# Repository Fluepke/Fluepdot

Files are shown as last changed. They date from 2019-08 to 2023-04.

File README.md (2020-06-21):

# Fluepdot
   

**Fluepdot** is a hardware and C project for controlling flip disc panels which where in use by the Berlin public transport operator **[BVG](https://www.bvg.de/en)**.

> This project was shown at [36C3](https://events.ccc.de/congress/2019/wiki/index.php/Main_Page). A large display was constructed from many flipdots. [Pictures](https://www.deutschlandfunkkultur.de/chaos-communication-congress-in-leipzig-auf-den-spuren-von.1264.de.html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) [of](https://foto.benedikt-geyer.de/fluepdot-36c3/) [the](https://www.korrupt.biz/7204/36c3-nachtraege/) [installation](https://www.astrastudio.de/cloud/index.php/apps/gallery/s/nDda9j8dZQ2oNMy#IMG_7059.jpeg).

## Documentation
For **documentation** and a **getting started**, please head over to [https://fluepdot.readthedocs.io/en/latest/](https://fluepdot.readthedocs.io/en/latest/).

## Hardware
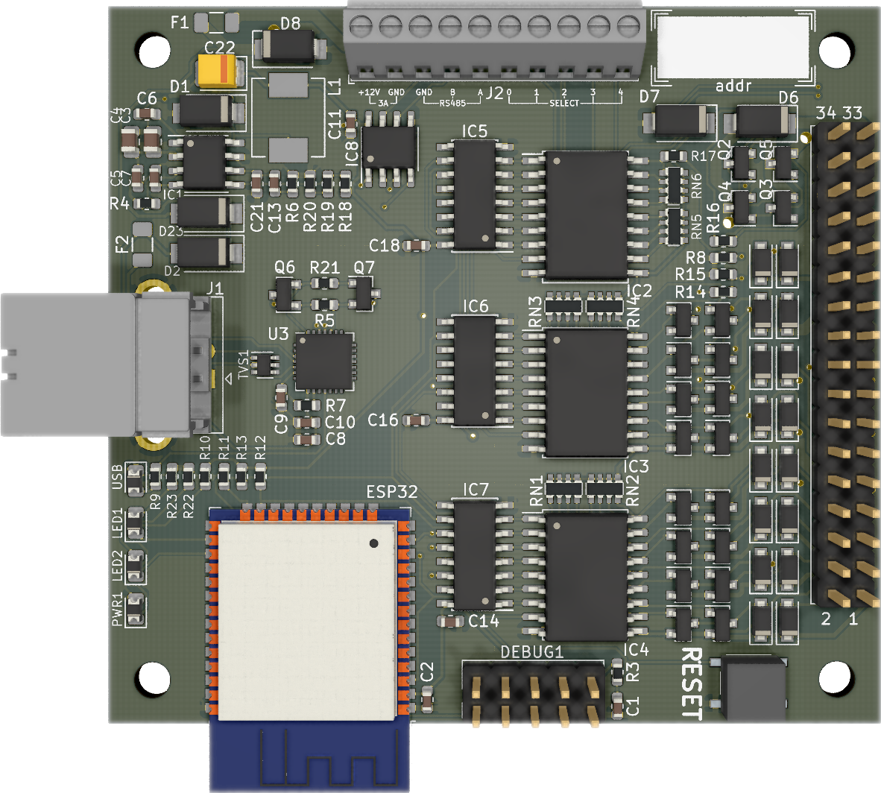
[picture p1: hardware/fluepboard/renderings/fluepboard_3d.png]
PCB 3D rendering


Flipdots and required HW  can be purchased by contacting [fluepdot-sales@luepke.email](mailto:fluepdot-sales@luepke.email).

## Firmware
You can download the latest standalone firmware installer [here](https://gitlab.com/fluepke/fluepdot/-/jobs/artifacts/master/raw/software/service_utility/service_utility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).

## License
Copyright (c) 2020, [@fluepke](http://twitter.com/fluepke) (Fabian Luepke)

Distributed under the terms of the GNU Affero General Public License version 3.

The full license is in the file LICENSE, distributed with this software.

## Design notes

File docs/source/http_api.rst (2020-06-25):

========
HTTP API
========

Framebuffer
===========

For simple integration into your projects, the *fluepboard* firmwares ships with a simple to use HTTP API.

Framebuffer encoding
--------------------

Framebuffers are **ASCII**-encoded. The only allowed characters are **<space>** ``0x20``, **X** ``0x58`` and **``\\n``** ``\0x0A``.

A **bright** (set) pixel is encoded as an X.

A **dark** (cleared) pixel is encoded as a space character.

Each line in a framebuffer has **exactly** the same amount of characters, which is **exactly** the *fluepdot's* width plus one newline character.

Each framebuffer has **exactly** 16 lines.

Lines are terminated by a single ``\n``. No carriage return is used.

Framebuffer manipulations
-------------------------

GET /framebuffer
^^^^^^^^^^^^^^^^
Params
    GET
        **None**
    POST
        **None**

Gets the current framebuffer encoded as explained above.
This endpoint can be used to calculate the framebuffer dimensions, thus there is no seperate endpoint for retrieving the geometry.

POST /framebuffer
^^^^^^^^^^^^^^^^^

Params
    GET
        **None**
    POST
        Raw framebuffer encoded as explained above

Draw the posted framebuffer to the *fluepdot*.

GET /pixel
^^^^^^^^^^

Params
    GET
        x - The x coordinate
        y - The y coordinate

Get the current pixel at the given coordinate encoded as above

POST /pixel
^^^^^^^^^^^

Params
    GET
        x
            The x coordinate (ascii encoded decimal value)
        y
            The y coordinate (ascii encoded decimal value)

Sets the pixel at the given coordinate to bright.

DELETE /pixel
^^^^^^^^^^^^^

Params
    GET
        x
            The x coordinate (ascii encoded decimal value)
        y
            The y coordinate (ascii encoded decimal value)

Set the pixel at the give coordinate to dark.

POST /framebuffer/text
^^^^^^^^^^^^^^^^^^^^^^

Params
    POST
        Text to display
    GET
        x
            The x coordinate to render text to
        y
            The y coordinate to render text to
        font
            The font's name to use for rendering text. Retrieve a list of fonts at `GET /fonts`

Render a string

GET /fonts
^^^^^^^^^^

Returns a list of installed fonts

For each font there are two lines: First the **full_name** and then **short_name** which is used with the `POST /framebuffer/text` eAPI endpoint.

Rendering options
=================

Rendering mode
--------------

GET /rendering/mode
^^^^^^^^^^^^^^^^^^^

Retuns an ASCII printed integer which value is defined as follows:

    .. doxygenenum:: flipdot_rendering_mode_t
       :project: fluepdot

PUT /rendering/mode
^^^^^^^^^^^^^^^^^^^
Params
    GET
        **None**
    POST
        ASCII printed integer, which value is to be interpreted as stated above.

Rendering timings encoding
--------------------------

Rendering timings are **ASCII**-encoded. The only allowed characters are 0-9 (``0x30-0x39``) and ``\\n``.

For each *fluepdot* column, there are **exactly** 3 rows:

1. **Pre delay**
   
    How long to wait (50 microseconds steps) before rendering to the column.

2. **Clear delay**

    How long to power the coils in order to clear the column (in 50 microseconds steps).

3. **Set delay**

    How long to power the coils in order to set the column (in 50 microseconds steps)

Each line has **exactly** 5 characters and one trailing ``\\n``. You have to pad with zeros.
Each line contains the decimal value in ascii-encoded form.

.. warning::

   Powering a coil repeatedly for a long duration *might* cause the coil to overheat and or fail.
   Decreasing the timings might result in higher **framerate**, but might result in not all pixels flipping.

   Usually **1600uS** are enough to reliably flip all pixels.
   This is the **default**.

GET /rendering/timings
^^^^^^^^^^^^^^^^^^^^^^

Returns the timing configuration encoded as explained above.

POST /rendering/timings
^^^^^^^^^^^^^^^^^^^^^^^

Params
    GET
        None
    POST
        Timing configuration as explained above.

Set the timing configuration.

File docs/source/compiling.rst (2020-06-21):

Compiling
=========

A multistage **Docker** environment is used to build firmware and documentation.

1. Clone the repository *recursively*.

   .. code:: bash

        git clone --recursive https://gitlab.com/fluepke/fluepdot.git

2. Build or pull the build container.

    * If you have a high bandwidth internet connection downloading is fastest (~ 10 GB):

        .. code:: bash
    
            docker pull fluepke/fluepdot-build-environment

    * If you have a low bandwidth internet connection building is faster (still ~ 3 GB)

        .. code:: bash
            
            docker build --force-rm -t fluepke/fluepdot-build-environment -f Dockerfile .

3. Build the second stage container

        .. code:: bash

            docker build --force-rm -t fluepdot -f Dockerfile.build .

4. Run the second stage container and flash the image (assuming your flipdot's serial device is at ``/dev/ttyUSB0``)

        .. code:: bash
           
            docker run -d --name fluepdot --device /dev/ttyUSB0:/fluepdot-device:rwm
            docker exec -it fluepdot \
                -w "/fluepdot/software/firmware" \
                -e ESPTOOL_PORT='/fluepdot-device' \
                -e ESPTOOL_BAUD='480000' \
                make flash

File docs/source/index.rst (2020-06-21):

.. Copyright (c) 2020, @fluepke (Fabian Luepke)

  Distributed under the terms of the GNU Affero General Public License version 3.

  The full license is in the file LICENSE, distributed with this software.




Hardware project for controlling legacy flipdot panels used by `BVG`_

Introduction
============

.. note::
   This project was exhibited at `36C3`_. A large display was constructed from many flipdots. `Pictures`_ `of`_ `the`_ `installation`_.

`fluepdot` is a hardware and C project for controlling flip disc panels which where in use by the Berlin public transport operator `BVG`_.

Hardware
--------
Up to 5 flipdot panels are managed by one *fluepboard*.
It is equipped with a dual core **ESP32** that supports **WLAN** and **Bluetooth**.
An **RS485** transceiver can be used for wired installations.
You only have to solder the THT (through hole technology) connectors which are shipped together with the fluepboard as a kit.

+----------+----------+
|     Top  |  Bottom  |
+----------+----------+
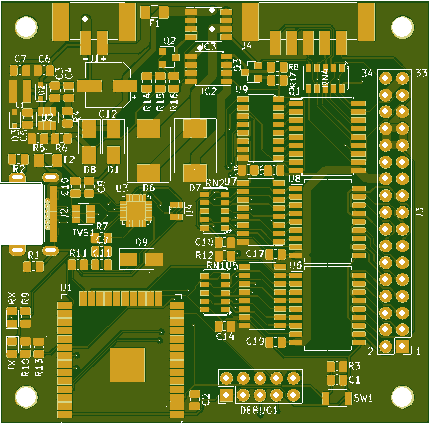
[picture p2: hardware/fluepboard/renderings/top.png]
PCB top layer
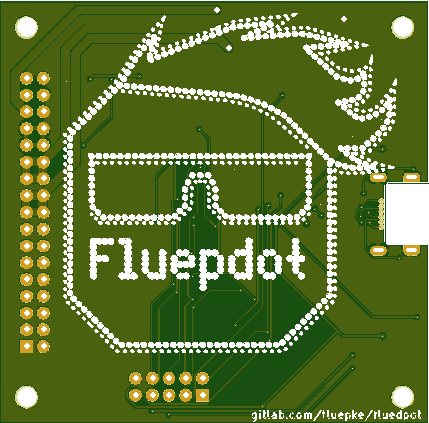
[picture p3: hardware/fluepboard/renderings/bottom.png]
PCB bottom layer
|     |  |
+----------+----------+

Software
--------
The *fluepboard* comes pre-flashed with a firmware, that allows for various ways of interacting with the flipdot.

Features:

- CLI for configuration and testing purposes
- mDNS for simple service discovery
- HTTP API for framebuffer manipulations
- SNMP for monitoring and framebuffer manipulations
- BT LE support for framebuffer manipulations
- C flipdot library for custom applications

.. toctree ::
   :caption: USAGE

   getting_started
   command_line
   snmp
   http_api

.. toctree ::
   :caption: FIRMWARE

   firmware_update

.. toctree ::
   :caption: DEVELOPER ZONE
   :maxdepth: 2

   compiling
   flipdot_library

.. _BVG: https://www.bvg.de/en
.. _36C3: https://events.ccc.de/congress/2019/wiki/index.php/Main_Page
.. _Pictures: https://www.deutschlandfunkkultur.de/chaos-communication-congress-in-leipzig-auf-den-spuren-von.1264.de.html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
.. _of: https://foto.benedikt-geyer.de/fluepdot-36c3/
.. _the: https://www.korrupt.biz/7204/36c3-nachtraege/
.. _installation: https://www.astrastudio.de/cloud/index.php/apps/gallery/s/nDda9j8dZQ2oNMy#IMG_7059.jpeg

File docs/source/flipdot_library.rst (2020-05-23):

Flipdot API reference
=====================

Flipdot
-------

Flipdot structs
^^^^^^^^^^^^^^^

.. doxygenstruct:: flipdot_t
   :project: fluepdot
   :members:

.. doxygenstruct:: flipdot_panel_t
   :project: fluepdot
   :members:

.. doxygenstruct:: flipdot_configuration_t
   :project: fluepdot
   :members:

Flipdot functions
^^^^^^^^^^^^^^^^^

.. doxygenfunction:: flipdot_initialize
   :project: fluepdot

.. doxygenfunction:: flipdot_set_power
   :project: fluepdot

.. doxygenfunction:: flipdot_get_power
   :project: fluepdot

.. doxygenfunction:: flipdot_set_dirty_flag
   :project: fluepdot

Framebuffer
-----------

Framebuffer struct
^^^^^^^^^^^^^^^^^^^
.. doxygenstruct:: framebuffer_t
   :project: fluepdot
   :members:

.. doxygenfunction:: flipdot_framebuffer_init
   :project: fluepdot

.. doxygenfunction:: flipdot_framebuffer_free
   :project: fluepdot

Framebuffer manipulation
^^^^^^^^^^^^^^^^^^^^^^^^
.. doxygenfunction:: flipdot_framebuffer_clear
   :project: fluepdot

.. doxygenfunction:: flipdot_framebuffer_get_pixel
   :project: fluepdot

.. doxygenfunction:: flipdot_framebuffer_set_pixel
   :project: fluepdot

Framebuffer de/encoding
^^^^^^^^^^^^^^^^^^^^^^^
.. doxygenfunction:: flipdot_framebuffer_encode_line
   :project: fluepdot

.. doxygenfunction:: flipdot_framebuffer_decode_line
   :project: fluepdot

.. doxygenfunction:: flipdot_framebuffer_encode_pixel
   :project: fluepdot

.. doxygenfunction:: flipdot_framebuffer_decode_pixel
   :project: fluepdot

.. doxygenfunction:: flipdot_framebuffer_printf
   :project: fluepdot

Framebuffer diffing
^^^^^^^^^^^^^^^^^^^

.. doxygenfunction:: flipdot_framebuffer_compare
   :project: fluepdot

.. doxygenfunction:: flipdot_framebuffer_compare_partial
   :project: fluepdot

Rendering options
-----------------

.. doxygenstruct:: flipdot_rendering_options_t
   :project: fluepdot
   :members:

.. doxygenstruct:: flipdot_rendering_delay_options_t
   :project: fluepdot
   :members:

.. doxygenenum:: flipdot_rendering_mode_t
   :project: fluepdot

.. doxygenfunction:: flipdot_rendering_options_initialize
   :project: fluepdot

.. doxygenfunction:: flipdot_rendering_options_copy
   :project: fluepdot

.. doxygenfunction:: flipdot_rendering_options_free
   :project: fluepdot

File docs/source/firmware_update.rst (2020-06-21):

Firmware update
===============

Using service utility
---------------------

The *fluepboard*'s firmware can be easily updated using a **standalone** binary for GNU/Linux (amd64) that is generated by the *Gitlab CI* build process of this project.

You can get the latest version `here`_.

Make sure your current user has permission to use the serial port (in this example `/dev/ttyUSB0`), then run:

    .. code:: bash

        ./service_utility -serial.port /dev/ttyUSB0

This utility will flash:
* the partition table
* the bootloader
* the factory application

Using esptool.py
----------------

You can also flash the firmware using `esptool.py`_. `Download`_ and unpack the compiled firmware, then run:

    .. code:: bash

        esptool.py --chip esp32 --before=default_reset --after=hard_reset write_flash --flash_mode dio --flash_freq 40m --flash_size 4MB 0x8000 partition_table/partition-table.bin 0x1000 bootloader/bootloader.bin 0x10000 flipdot-firmware.bin

.. _here: https://gitlab.com/fluepke/fluepdot/-/jobs/artifacts/master/raw/software/service_utility/service_utility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
.. _esptool.py: https://github.com/espressif/esptool
.. _Download: https://gitlab.com/fluepke/fluepdot/-/jobs/artifacts/master/download?job=build_esp32_image

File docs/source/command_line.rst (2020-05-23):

Commandline interface
=====================

For debugging and configuration purposes the *fluepboard* firmware provides a simple CLI.

The serial interface is available by connecting the *fluepboard* to a computer via USB.

Serial interface works at 115200/8-N-1 [#]_.

.. note::
   
    After performing configuration changes, please issue a ``config_save`` followed by a ``reboot`` in order to apply the configuration.

Available commands
------------------

Type ``help`` to get a list of available commands:

.. code:: bash

    help
      Print the list of registered commands
    
    ping  [-W <t>] [-i <t>] [-s <n>] [-c <n>] [-Q <n>] <host>
      send ICMP ECHO_REQUEST to network hosts
      -W, --timeout=<t>  Time to wait for a response, in seconds
      -i, --interval=<t>  Wait interval seconds between sending each packet
      -s, --size=<n>  Specify the number of data bytes to be sent
      -c, --count=<n>  Stop after sending count packets
      -Q, --tos=<n>  Set Type of Service related bits in IP datagrams
            <host>  Host address
    
    host  <host>
      Perform a DNS lookup
            <host>  Host to look up
    
    traceroute  <host>
      Perform a traceroute
            <host>  Host to traceroute
    
    reboot
      Perform a software reset
    
    show_version
      Get version of chip and SDK
    
    show_tasks
      Get information about running tasks
    
    config_save
      Save the current system configuration to flash
    
    config_load
      Load the system configuration from flash
    
    config_show
      Show the current system configuration
    
    config_reset
      Factory reset the system configuration
    
    config_wifi_ap  <ssid> [<password>]
      Configure AP mode
            <ssid>  WiFi SSID
        <password>  WiFi Password
    
    config_wifi_station  <ssid> [<password>]
      Configure station mode
            <ssid>  WiFi SSID
        <password>  WiFi Password
    
    config_hostname  <hostname>
      Set system hostname
        <hostname>  Hostname
    
    config_panel_layout  <panel_size> [<panel_size>]...
      Configure panel count and sizes
      <panel_size>  Panel size
    
    flipdot_clear  [--invert]
      Clear the flipdot
          --invert  Set all pixels to white instead of black
    
    show_fonts
      List installed fonts
    
    render_font  [-x <int>] [-y <int>] [-f <font>] <text>
      Render some text given some font
      -x, --X=<int>  Depending on aligned, either left, center or right edge of target.
      -y, --Y=<int>  Upper edge of the target area.
      -f, --font=<font>  Name of font to use
            <text>  Text to display
    
Usage examples
--------------

- Connect to a wireless network

    .. code:: bash
    
       config_wifi_station NetworkName Password
       config_show
       config_save
       reboot

- Connect to an unencrypted wireless network

    .. code:: bash
    
       config_wifi_station NetworkName
       config_show
       config_save
       reboot

- MTU test

    .. code:: bash

        ping fritz.box -s 1472

- Cycle all pixels

    .. code:: bash

        flipdot_clear
        flipdot_clear --invert

Footnotes
---------

.. [#] See https://en.wikipedia.org/wiki/8-N-1

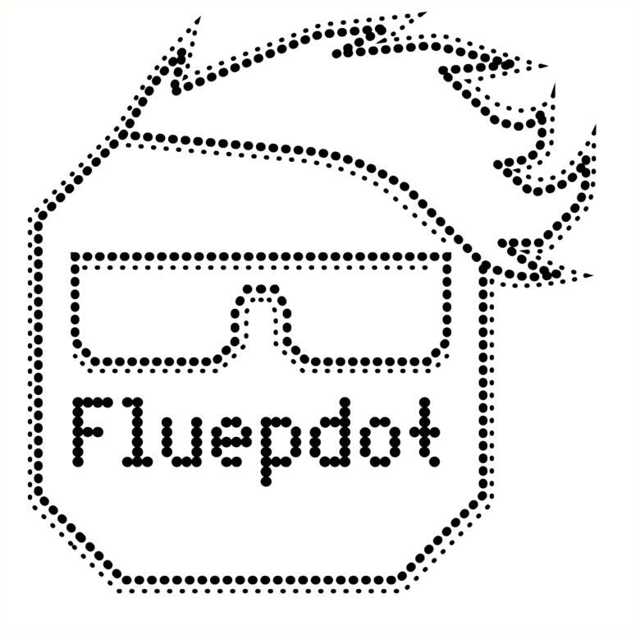
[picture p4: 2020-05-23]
artwork/output.png

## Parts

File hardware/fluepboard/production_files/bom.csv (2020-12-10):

Comment | Designator | Footprint | LCSC | LCSC | Octopart | Description | Extended Part | Manufacturer | Height | LCSC Price/Stock | Manufacturer_Name | Manufacturer_Part_Number | Category | DK_Datasheet_Link | DK_Detail_Page | Digi-Key_PN | Family | MPN | status | Status
100nF | C1,C2,C11,C6,C9,C8,C18,C16,C14 | Capacitor_SMD:C_0603_1608Metric |  | C14663 | C0805C104Z5VACTU | MULTILAYER CERAMIC CAPACITORS MLCC - SMD/SMT 100NF 50V 0603 ROHS | 0 | CC0603KRX7R9BB104
1uF | C10 | Capacitor_SMD:C_0603_1608Metric |  | C15849 |  | MULTILAYER CERAMIC CAPACITORS MLCC - SMD/SMT 1UF 50V 0603 ROHS | 0 | CL10A105KB8NNNC
1nF | C13 | Capacitor_SMD:C_0603_1608Metric |  | C1588 |  | MULTILAYER CERAMIC CAPACITORS MLCC - SMD/SMT 1NF 50V 0603 ROHS | 0 | CL10B102KB8NNNC
47pF | C21 | Capacitor_SMD:C_0603_1608Metric |  | C1671 |  | MULTILAYER CERAMIC CAPACITORS MLCC - SMD/SMT 47PF 50V 0603 ROHS | 0 | CL10C470JB8NNNC
100uF | C22 | Capacitor_Tantalum_SMD:CP_EIA-3528-21_Kemet-B |  | C16133 |  | TANTALUM CAPACITORS 100UF 6.3V CASE-B_3528 ROHS | 0 | TAJB107K006RNJ
4.7uF | C4,C3 | Capacitor_SMD:C_0805_2012Metric |  | C1779 |  | MULTILAYER CERAMIC CAPACITORS MLCC - SMD/SMT 4.7UF 25V 0805 ROHS | 0 | CL21A475KAQNNNE
10nF | C5,C7 | Capacitor_SMD:C_0603_1608Metric |  | C57112 |  | MULTILAYER CERAMIC CAPACITORS MLCC - SMD/SMT 10NF 50V 0603 ROHS | 0 | 0603B103K500NT
SS14 | D2,D23 | Diode_SMD:D_SMA |  | C2480 |  | SCHOTTKY BARRIER DIODES (SBD) SMA(DO-214AC) ROHS | 0 | SS14
SM4007PL | D3,D9,D11,D13,D15,D17,D19,D21,D5,D10,D12,D14,D16,D18,D20,D22 | Diode_SMD:D_SOD-123F |  | C64898 |  |  |  | SM4007PL
USB | D4 | Diode_SMD:D_0805_2012Metric |  | C2296 | SML-211YTT86 | LIGHT EMITTING DIODES (LED) YELLOW 592~594NM 95~113MCD@20MA TOP VIEW 0805 ROHS | 0 | 17-21SUYC/TR8
SS34 | D8,D1,D6,D7 | Diode_SMD:D_SMA |  | C84635 | B140-E3/61T | SCHOTTKY BARRIER DIODES (SBD) SMA(DO-214AC) ROHS | 0 | SS34
Conn_02x05_Counter_Clockwise | DEBUG1 | Connector_PinHeader_2.54mm:PinHeader_2x05_P2.54mm_Vertical |  |  | Molex 10-89-7101
ESP32-WROOM-32 | ESP32 | RF_Module:ESP32-WROOM-32 |  | - | ESP32-WROOM-32
3A | F1 | Fuse:Fuse_1206_3216Metric |  | C182441 |  | SURFACE MOUNT FUSES 1206 ROHS | 1 | 12D1300C
500mA | F2 | Fuse:Fuse_1206_3216Metric |  | C69688 | 3413.0113.22 | PTC RESETTABLE FUSES 1206 ROHS | 1 | nSMD050
MountingHole | H1,H3,H4,H2 | MountingHole:MountingHole_3.2mm_M3_ISO7380
TPS54331DR | IC1 | Package_SO:SOIC-8_3.9x4.9mm_P1.27mm |  | C9865 |  | DC-DC CONVERTERS STEP-DOWN ADJUSTABLE 1 3.5V 28V 0.8V 25V 3A SOIC-8_150MIL ROHS | 0 | TPS54331DR
ULN2803ADWR | IC2,IC4,IC3 | Package_SO:SOIC-18W_7.5x11.6mm_P1.27mm |  | C9683 | ULN2803ADW | TRANS 8NPN DARL 50V 0.5A 18SO | 0 | ULN2803ADWR |  |  |  |  | Discrete Semiconductor Products | http://www.ti.com/lit/ds/symlink/uln2803a.pdf | /product-detail/en/texas-instruments/ULN2803ADWR/296-15777-1-ND/598088 | 296-15777-1-ND | Transistors - Bipolar (BJT) - Arrays | ULN2803ADWR | review
74HCT595 | IC7,IC6,IC5 | Package_SO:SOIC-16_3.9x9.9mm_P1.27mm |  | C5947 | MC74HC595ADG |  | 0
SP3485EN | IC8 | Package_SO:SOIC-8_3.9x4.9mm_P1.27mm |  | C8963 |  |  | 0 | CP2102-GMR
USB_B | J1 | Connector_USB:USB_B_OST_USB-B1HSxx_Horizontal |  | C46392
Conn_01x10_Female | J2 | fluepdot:TerminalBlock_Phoenix_MPT-0,5-10-2.54_1x10_P2.54mm_Horizontal
Conn_02x17_Odd_Even | J3 | Connector_PinHeader_2.54mm:PinHeader_2x17_P2.54mm_Vertical |  |  | XG4A-3431
8.2uH | L1 | fluepdot:SMD-PIND-6.6x7.1x3.0_1.6x3.0 |  | C132140 |  | POWER INDUCTORS 8.2UH ±20% 5A SMD,6.6X7.1X3.0MM ROHS | 1 | MWSA0603-8R2MT
LED1 | LED1 | Diode_SMD:D_0805_2012Metric |  | C2296 |  | LIGHT EMITTING DIODES (LED) YELLOW 592~594NM 95~113MCD@20MA TOP VIEW 0805 ROHS | 0 | 17-21SUYC/TR8
LED2 | LED2 | Diode_SMD:D_0805_2012Metric |  | C2296 |  | LIGHT EMITTING DIODES (LED) YELLOW 592~594NM 95~113MCD@20MA TOP VIEW 0805 ROHS | 0 | 17-21SUYC/TR8
PWR | PWR1 | Diode_SMD:D_0805_2012Metric |  | C2296 |  | LIGHT EMITTING DIODES (LED) YELLOW 592~594NM 95~113MCD@20MA TOP VIEW 0805 ROHS | 0 | 17-21SUYC/TR8
SS8550 | Q3 | Package_TO_SOT_SMD:SOT-23 |  | C8542 |  | TRANSISTORS (NPN/PNP) PNP 1.5A 25V SOT-23(SOT-23-3) ROHS | 0 | SS8550
AO3400A | Q4 | Package_TO_SOT_SMD:SOT-23 |  | C20917 |  | MOSFET N TRENCH 30V 5.7A 1.5V @ 250UA 26.5 M? @ 5.7A,10V SOT-23-3L ROHS | 0 | AO3400A
SS8050 | Q6,Q7,Q2 | Package_TO_SOT_SMD:SOT-23 |  | C2150 |  | TRANSISTORS (NPN/PNP) NPN 1.5A 25V SOT-23(SOT-23-3) ROHS | 0
AO3401A | Q8,Q10,Q12,Q14,Q16,Q18,Q20,Q22,Q9,Q11,Q13,Q15,Q17,Q19,Q21,Q23,Q5 | Package_TO_SOT_SMD:SOT-23 |  | C15127 |  | MOSFET P TRENCH 30V 4A 1.3V @ 250UA 44 M? @ 4.3A,10V SOT-23-3L ROHS | 0 | AO3401A
470R | R14 | Resistor_SMD:R_0603_1608Metric |  | C23179 | RC0805FR-07470RL | CHIP RESISTOR - SURFACE MOUNT 470OHMS ±1% 1/10W 0603 ROHS | 0 | 0603WAF4700T5E
1k | R17 | Resistor_SMD:R_0603_1608Metric |  | C21190 | RC0805FR-071K | CHIP RESISTOR - SURFACE MOUNT 1KOHMS ±1% 1/10W 0603 ROHS | 0 | 0603WAF1001T5E
3k | R19 | Resistor_SMD:R_0603_1608Metric |  | C4211 |  | CHIP RESISTOR - SURFACE MOUNT 3KOHMS ±1% 1/10W 0603 ROHS | 0 | 0603WAF3001T5E
240 | R20 | Resistor_SMD:R_0603_1608Metric |  | C23350 |  | CHIP RESISTOR - SURFACE MOUNT 240OHMS ±1% 1/10W 0603 ROHS | 0 | 0603WAF2400T5E
270 | R23,R22,R10 | Resistor_SMD:R_0603_1608Metric |  | C22966 |  | CHIP RESISTOR - SURFACE MOUNT 270OHMS ±1% 1/10W 0603 ROHS | 0 | 0603WAF2700T5E
10k | R3,R4,R18,R11,R5,R21,R12,R13,R8,R16,R15 | Resistor_SMD:R_0603_1608Metric |  | C25804 | RC0805FR-0710KL | CHIP RESISTOR - SURFACE MOUNT 10KOHMS ±1% 1/10W 0603 ROHS | 0 | 0603WAF1002T5E
30k | R6 | Resistor_SMD:R_0603_1608Metric |  | C22984 |  | CHIP RESISTOR - SURFACE MOUNT 30KOHMS ±1% 1/10W 0603 ROHS | 0 | 0603WAF1002T5E
4.7k | R7 | Resistor_SMD:R_0603_1608Metric |  | C23162 |  | CHIP RESISTOR - SURFACE MOUNT 4.7KOHMS ±1% 1/10W 0603 ROHS | 0 | 0603WAF4701T5E
270R | R9 | Resistor_SMD:R_0603_1608Metric |  | C22966 | RC0805FR-07270RL | CHIP RESISTOR - SURFACE MOUNT 270OHMS ±1% 1/10W 0603 ROHS | 0 | 0603WAF2700T5E
R_Pack04 | RN5,RN6,RN1,RN2,RN3,RN4 | Resistor_SMD:R_Array_Convex_4x0603 |  | C29718 |  | RESISTOR NETWORKS & ARRAYS 10KOHMS ±5% 1/16W 0603_X4 ROHS | 0 | 4D03WGJ0103T5E
TS-1187A-B-A-B | S1 | TS-1187A-B-A-B:TS1187ABAB |  | C318884 |  | Tactile Switches SPST 5.10mm x 5.10mm 0.40mm 50mA @ 12VDC SMD RoHS | 1 | TS-1187A-B-A-B | 4.05 | https://lcsc.com/product-detail/Tactile-Switches_XKB-Enterprise-TS-1187-B-A-A_C318884.html | XKB Enterprise | TS-1187A-B-A-B
SMF05CT1G | TVS1 | Package_TO_SOT_SMD:SOT-363_SC-70-6 |  | C15879 |  | TVS SC-70-6(SOT-363) ROHS | 0 | SMF05CT1G
CP2102N-A01-GQFN28 | U3 | Package_DFN_QFN:QFN-28-1EP_5x5mm_P0.5mm_EP3.35x3.35mm |  | C6568 |  | USB 1/1 1MBPS 3V ~ 3.6V QFN-28_5X5X05P ROHS | 0

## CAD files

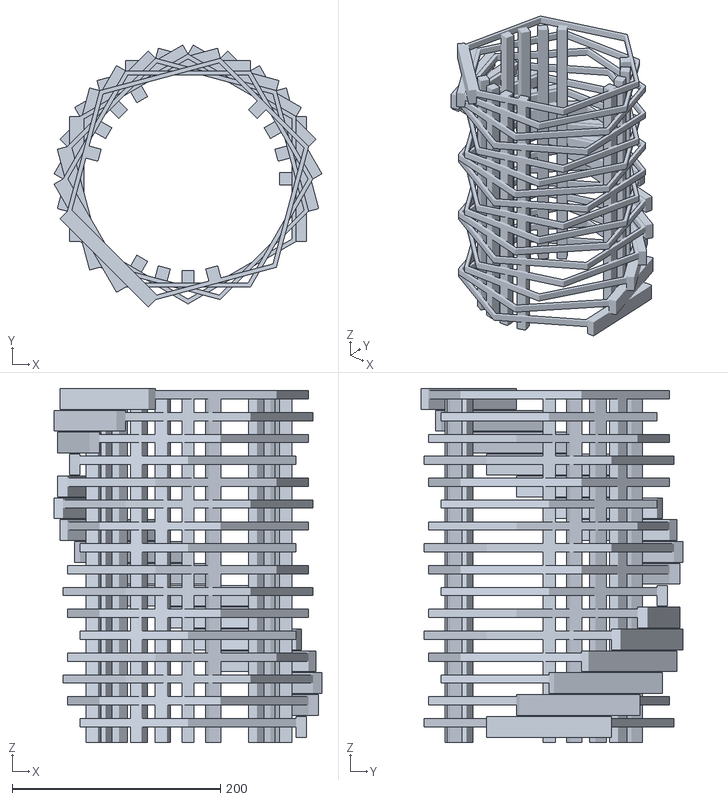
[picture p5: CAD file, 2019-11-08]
artwork/hexagon.stl
257.3 x 251.6 x 340.0

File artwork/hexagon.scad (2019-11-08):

side_h = 21;
side_h_strut = 8;
side_w = 120;
side_d = 4;
side_h_offx = 15;
strut_w = 12;
strut_d = strut_w;
r = sqrt(3)/2*side_w;
rep_cnt = 4;
angle = 60/rep_cnt;
layers = 16;
display_h = 20;
display_w = 120;
display_d = 10;
display_offx = 5;
num_elems = 60/angle * layers/rep_cnt;
strut_h = side_h * num_elems;

strut_angle = 120;

for (b = [0 : strut_angle : 360-strut_angle]) {
    rotate([0, 0, b]) {
        for (a = [0 : 15 : 45]) {
            rotate([0, 0, a])
            translate([r-side_d-strut_d, -strut_w/2, 0])
            cube([strut_d, strut_w, strut_h]);
        }
    }
}

for (i = [0 : num_elems-1]) {
    translate([0, 0, side_h_offx + side_h * i])
    rotate([0, 0, angle*i]) {
        for (a = [0 : 60 : 300]) {
            rotate([0, 0, a])
            translate([r-side_d, -side_w/2, 0])
            cube([side_d, side_w, side_h_strut]);
        }
    }
}

color([0.8, 0.8, 0])
for (i = [0 : num_elems-1]) {
    translate([0, 0, display_offx + side_h * i])
    rotate([0, 0, angle*i]) {
        rotate([0, 0, a])
        translate([r, -display_w/2, 0])
        cube([display_d, display_w, display_h]);
    }
}

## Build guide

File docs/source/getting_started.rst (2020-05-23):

Getting started
===============

This short guide explains how to get from receiving a *fluepdot* kit to flipping pixels the first time.

Hardware assembly
-----------------
.. warning::
   Electrons'n'stuff can be dangerous. Use your brain and a proper 12V power supply rated for at least 3 amperes.

Perform the following steps:

0. Solder the components **J1** (USB port), **J2** (10 pins, 2.54mm, power supply, RS485 and select) and **J3** (34 pins, flat cable connector) to the board.

   Fluepboard 3d rendering
   
      J3 notch must point to the right, to the PCB's border.

1. Attach the flatband cable to the boards and the fluepboard.

2. Connect the panel's select pins to the PCB. Pinout is given in the rendering.
   The order is left (0) to right (5), assuming panel's "top" is where the very long connector with huge amounts of pins is.

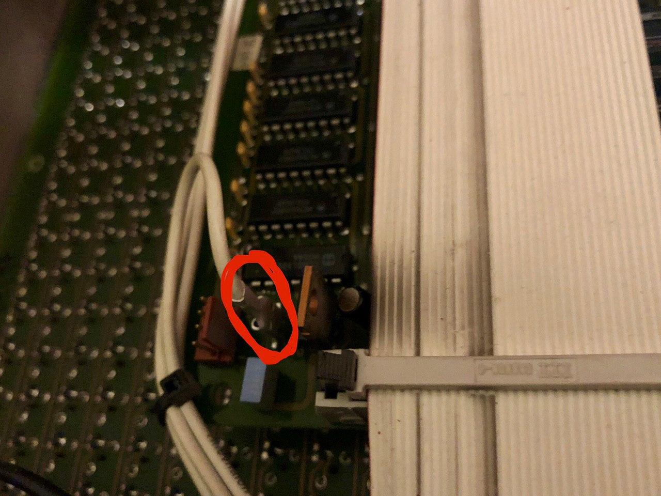
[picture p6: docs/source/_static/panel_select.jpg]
Panel select
   
   
      Panel select pin (highlighted)

   In case you mess with the panel order, there are CLI commands for changing the order in software.

3. Provide 12V and at least 3A to the PCB as displayed on the pinout above.

4. Connect the *fluepboard* via USB to some computer.

Software
--------
The *fluepboard* has the USB vendor id **0x1209** and product id **0x4223** assigned by `pid.codes`_.

Please configure your system (e.g. by writing a udev rule) to allow access to the serial port.

USB-to-serial chip in use is a **CP2102N**. Users of linux based operating systems don't need to install any drivers.

.. note::

   Serial interface params

    - **Baudrate**: 115200
    - **Data Bits**: 8
    - **Parity**: None
    - **Stop Bits**: 1

0. Connect to the serial interface

   .. code:: bash

    screen /dev/ttyUSB0 115200

1. Configure the fluepdot panel layout

   .. code:: bash

    TODO

2. *Optional*: Set a hostname

   .. code:: bash

    config_hostname yet_another_iot_device.local
 
3. *Optional*: Connect to a wireless LAN

   .. code:: bash

    config_wifi_station  <ssid> [<password>]
     Configure station mode
           <ssid>  WiFi SSID
       <password>  WiFi Password

   .. warning::
      Absolutely no attempt to protect your wireless LAN's credentials is made.
      Everyone having access to the fluepboard can retrieve them easily.

      The fluepboard's firmware intentionally does not provide means of **authentication**.
      It is up to you as a network operator to restrict access (e.g. by **firewalling**).

4. Save the configuration and reboot

   .. code:: bash

    config_show
    config_save
    reboot

5. Clear and set all pixels as a test, be prepared for noise

   .. code:: bash

    flipdot_clear --invert
    flipdot_clear

.. _pid.codes: http://pid.codes/1209/4223/

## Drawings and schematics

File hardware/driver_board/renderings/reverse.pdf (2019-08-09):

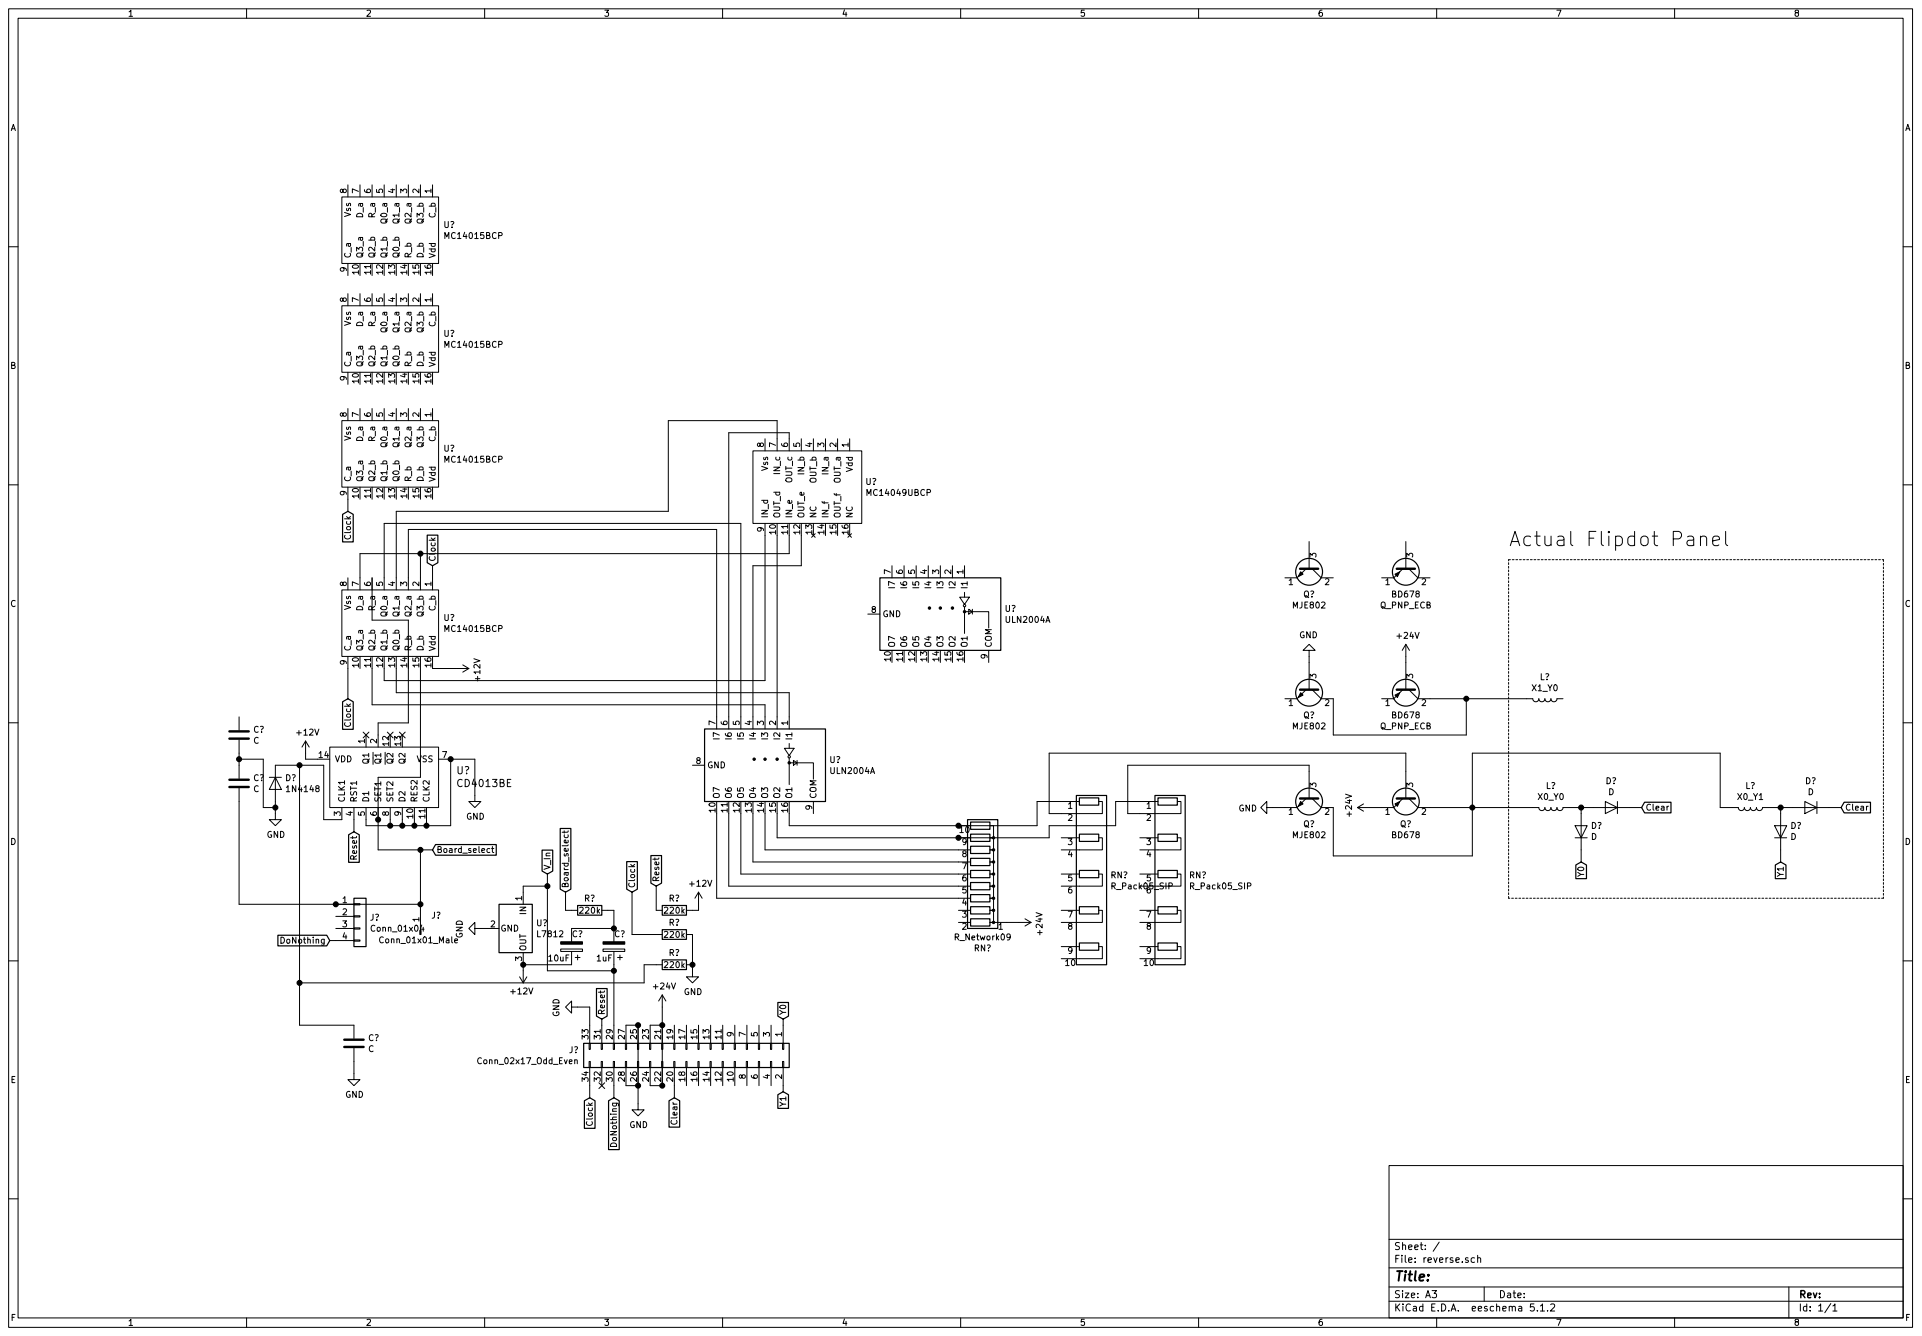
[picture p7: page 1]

1 GND 2 OUT
Id: 1/1 Title: File: reverse.sch Sheet: / IN

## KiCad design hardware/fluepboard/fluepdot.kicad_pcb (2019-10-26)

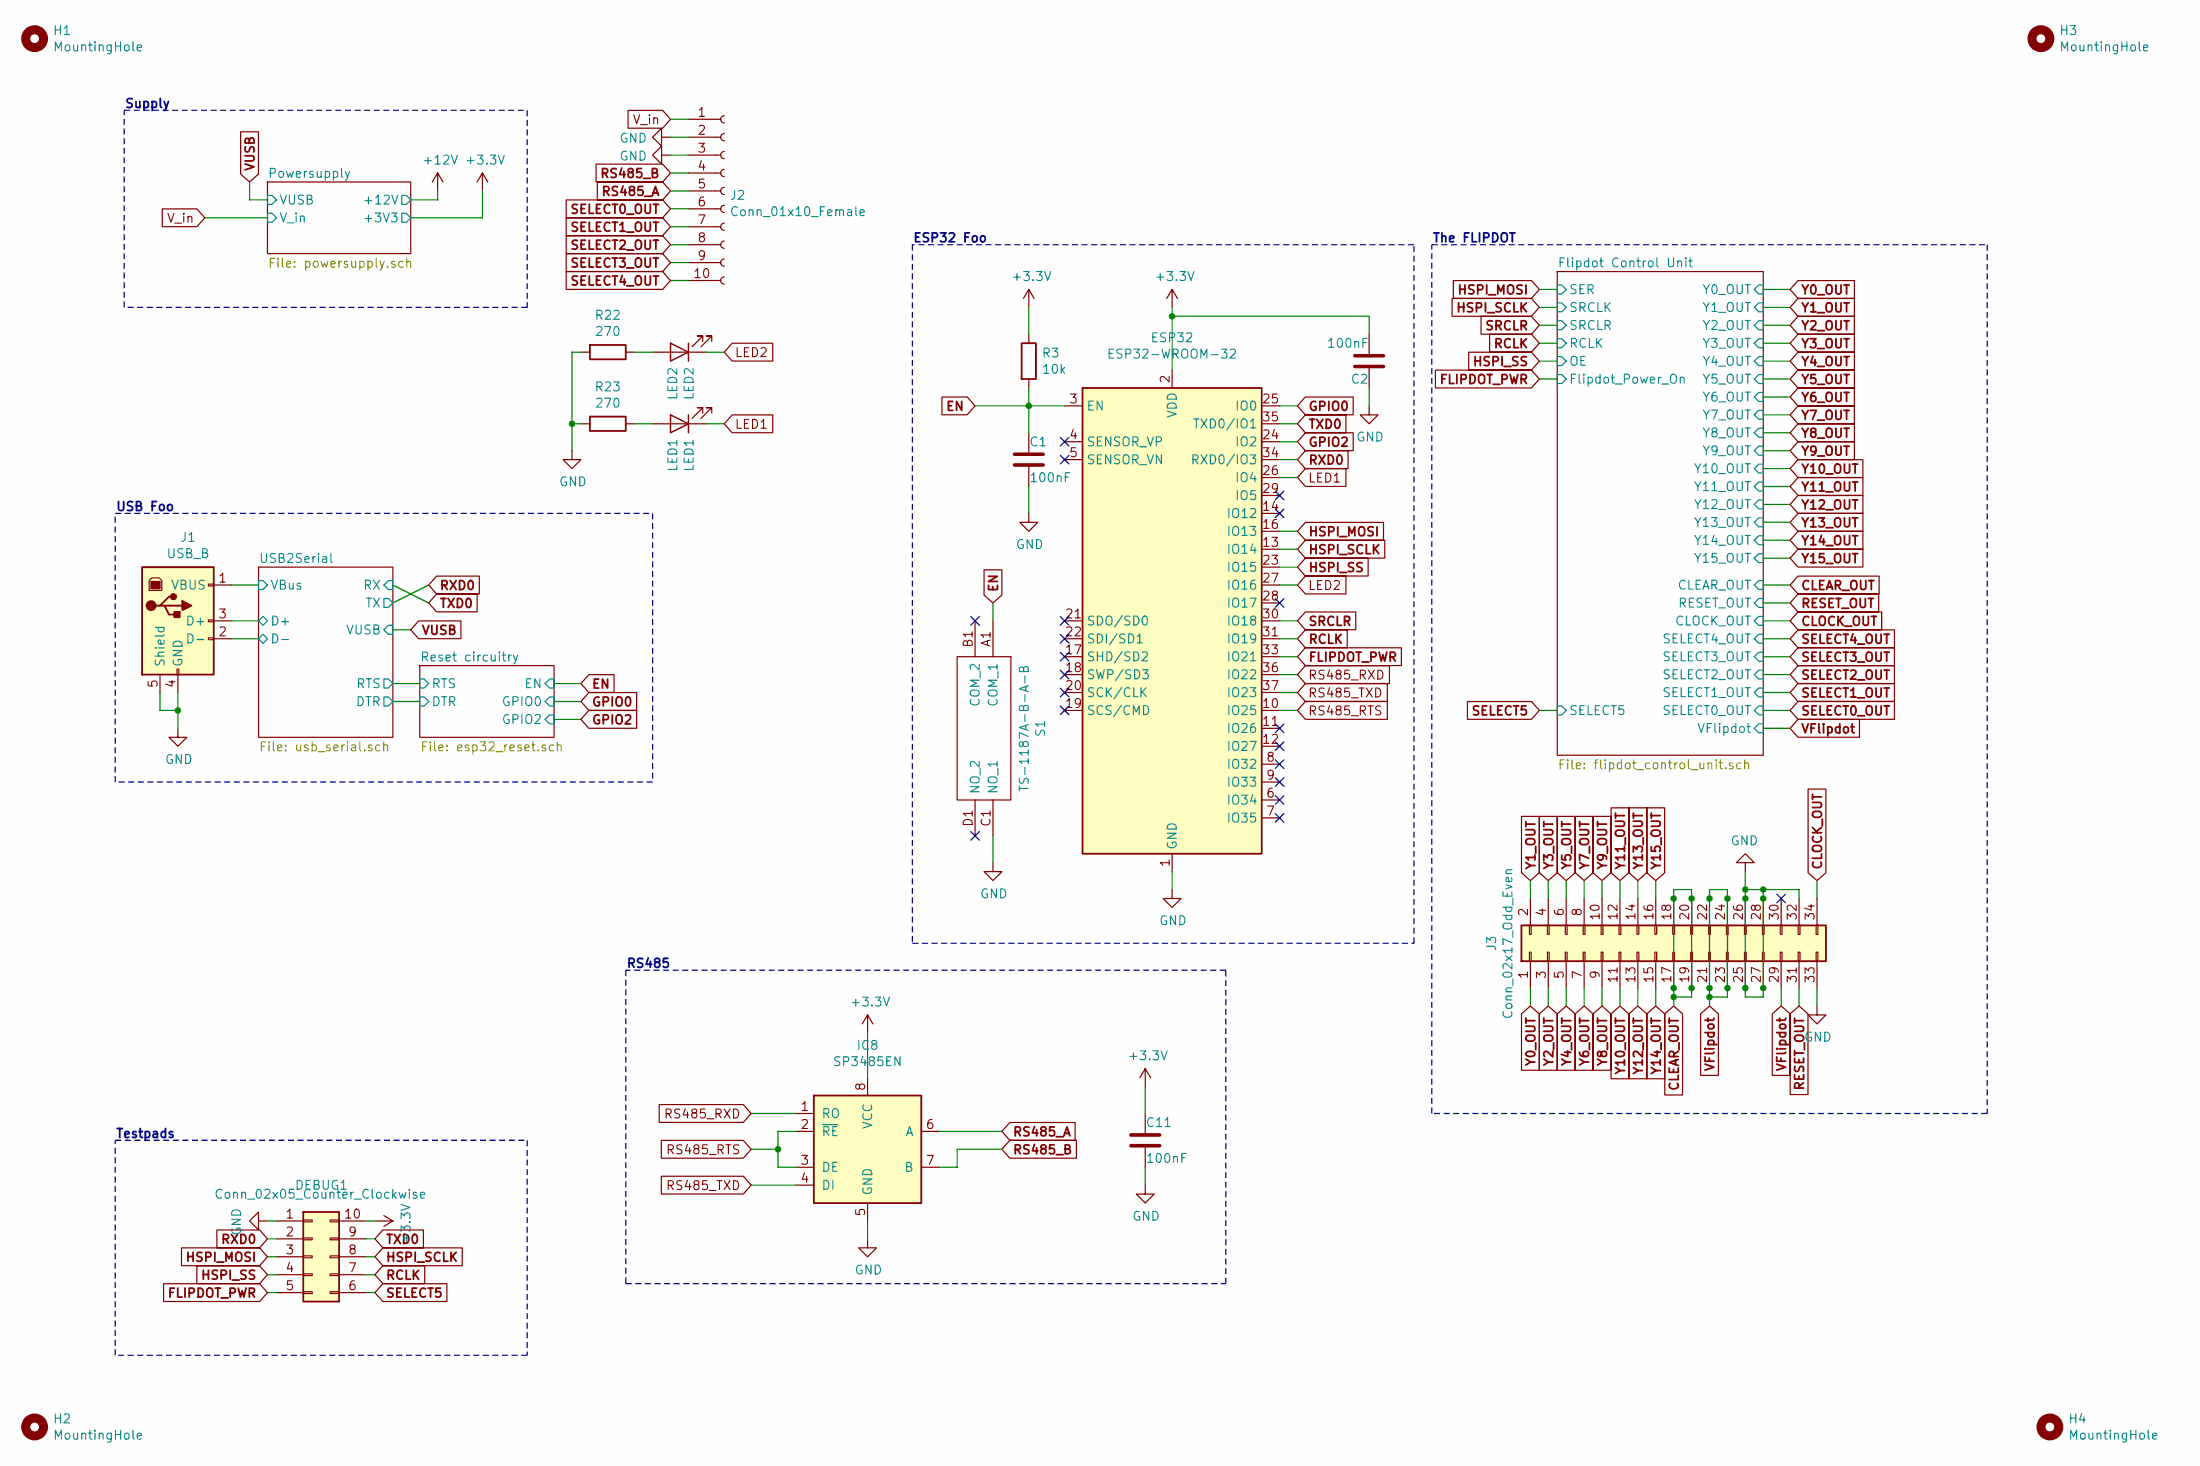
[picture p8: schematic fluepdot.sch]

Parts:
C1, C2, C11: 100nF; C_0603_1608Metric; LCSC C14663
DEBUG1: Conn_02x05_Counter_Clockwise; PinHeader_2x05_P2.54mm_Vertical
ESP32: ESP32-WROOM-32
H1, H2, H3, H4: MountingHole; MountingHole_3.2mm_M3_ISO7380
IC8: SP3485EN; SOIC-8_3.9x4.9mm_P1.27mm; LCSC C8963
J1: USB_B; USB_B_OST_USB-B1HSxx_Horizontal; LCSC C46392
J2: Conn_01x10_Female; TerminalBlock_Phoenix_MPT-0,5-10-2.54_1x10_P2.54mm_Horizont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
J3: Conn_02x17_Odd_Even; PinHeader_2x17_P2.54mm_Vertical
LED1: LED1; D_0805_2012Metric; LCSC C2296
LED2: LED2; D_0805_2012Metric; LCSC C2296
R3: 10k; R_0603_1608Metric; LCSC C25804
R22, R23: 270; R_0603_1608Metric; LCSC C22966
S1: TS-1187A-B-A-B; TS1187ABAB; Manufacturer_Part_Number TS-1187A-B-A-B; LCSC C318884

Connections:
+3V3: C2.2, C11.1, DEBUG1.10, ESP32.2 (VDD), IC8.8 (VCC), R3.1; also elsewhere on the board
/USB2Serial/D+: J1.3 (D+); also elsewhere on the board
/USB2Serial/D-: J1.2 (D-); also elsewhere on the board
/USB2Serial/VBus: J1.1 (VBUS); also elsewhere on the board
CLEAR_OUT: J3.17, J3.18, J3.19, J3.20; also elsewhere on the board
CLOCK_OUT: J3.34; also elsewhere on the board
EN: C1.1, ESP32.3 (EN), R3.2, S1.A1 (COM_1); also elsewhere on the board
FLIPDOT_PWR: DEBUG1.5, ESP32.33 (IO21); also elsewhere on the board
GND: C1.2, C2.1, C11.2, DEBUG1.1, ESP32.1 (GND), ESP32.15 (GND), ESP32.38 (GND), IC8.5 (GND), J1.4 (GND), J1.5 (Shield), J2.2, J2.3, J3.25, J3.26, J3.27, J3.28, J3.32, J3.33, R22.2, R23.2, S1.C1 (NO_1); also elsewhere on the board
GPIO0: ESP32.25 (IO0); also elsewhere on the board
GPIO2: ESP32.24 (IO2); also elsewhere on the board
HSPI_MOSI: DEBUG1.3, ESP32.16 (IO13); also elsewhere on the board
HSPI_SCLK: DEBUG1.8, ESP32.13 (IO14); also elsewhere on the board
HSPI_SS: DEBUG1.4, ESP32.23 (IO15); also elsewhere on the board
LED1: ESP32.26 (IO4), LED1.1 (K)
LED2: ESP32.27 (IO16), LED2.1 (K)
unnamed: LED1.2 (A), R23.1
unnamed: LED2.2 (A), R22.1
RCLK: DEBUG1.7, ESP32.31 (IO19); also elsewhere on the board
RESET_OUT: J3.31; also elsewhere on the board
RS485_A: IC8.6 (A), J2.5
RS485_B: IC8.7 (B), J2.4
RS485_RTS: ESP32.10 (IO25), IC8.2 (~RE~), IC8.3 (DE)
RS485_RXD: ESP32.36 (IO22), IC8.1 (RO)
RS485_TXD: ESP32.37 (IO23), IC8.4 (DI)
RXD0: DEBUG1.2, ESP32.34 (RXD0/IO3); also elsewhere on the board
SELECT0_OUT: J2.6; also elsewhere on the board
SELECT1_OUT: J2.7; also elsewhere on the board
SELECT2_OUT: J2.8; also elsewhere on the board
SELECT3_OUT: J2.9; also elsewhere on the board
SELECT4_OUT: J2.10; also elsewhere on the board
SELECT5: DEBUG1.6; also elsewhere on the board
SRCLR: ESP32.30 (IO18); also elsewhere on the board
TXD0: DEBUG1.9, ESP32.35 (TXD0/IO1); also elsewhere on the board
VFlipdot: J3.21, J3.22, J3.23, J3.24, J3.29; also elsewhere on the board
V_in: J2.1; also elsewhere on the board
Y0_OUT: J3.1; also elsewhere on the board
Y1_OUT: J3.2; also elsewhere on the board
Y2_OUT: J3.3; also elsewhere on the board
Y3_OUT: J3.4; also elsewhere on the board
Y4_OUT: J3.5; also elsewhere on the board
Y5_OUT: J3.6; also elsewhere on the board
Y6_OUT: J3.7; also elsewhere on the board
Y7_OUT: J3.8; also elsewhere on the board
Y8_OUT: J3.9; also elsewhere on the board
Y9_OUT: J3.10; also elsewhere on the board
Y10_OUT: J3.11; also elsewhere on the board
Y11_OUT: J3.12; also elsewhere on the board
Y12_OUT: J3.13; also elsewhere on the board
Y13_OUT: J3.14; also elsewhere on the board
Y14_OUT: J3.15; also elsewhere on the board
Y15_OUT: J3.16; also elsewhere on the board

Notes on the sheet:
Testpads
USB Foo
Supply
ESP32 Foo
The FLIPDOT
RS485

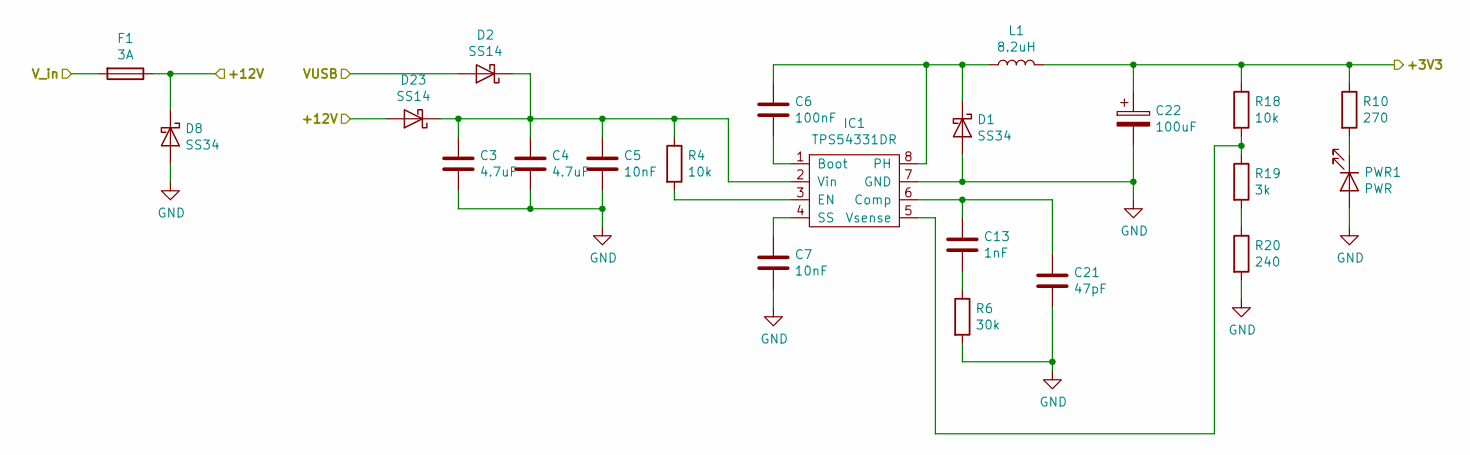
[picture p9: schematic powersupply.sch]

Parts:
C3, C4: 4.7uF; C_0805_2012Metric; LCSC C1779
C5, C7: 10nF; C_0603_1608Metric; LCSC C57112
C6: 100nF; C_0603_1608Metric; LCSC C14663
C13: 1nF; C_0603_1608Metric; LCSC C1588
C21: 47pF; C_0603_1608Metric; LCSC C1671
C22: 100uF; CP_EIA-3528-21_Kemet-B; LCSC C16133
D1, D8: SS34; D_SMA; LCSC C84635
D2, D23: SS14; D_SMA; LCSC C2480
F1: 3A; Fuse_1206_3216Metric; LCSC C182441
IC1: TPS54331DR; SOIC-8_3.9x4.9mm_P1.27mm; LCSC C9865
L1: 8.2uH; SMD-PIND-6.6x7.1x3.0_1.6x3.0; LCSC C132140
PWR1: PWR; D_0805_2012Metric; LCSC C2296
R4, R18: 10k; R_0603_1608Metric; LCSC C25804
R6: 30k; R_0603_1608Metric; LCSC C22984
R10: 270; R_0603_1608Metric; LCSC C22966
R19: 3k; R_0603_1608Metric; LCSC C4211
R20: 240; R_0603_1608Metric; LCSC C23350

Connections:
+3V3: C22.1, L1.2, R10.1, R18.1; also elsewhere on the board
+12V: D8.1 (K), D23.2 (A), F1.1; also elsewhere on the board
GND: C3.2, C4.2, C5.2, C7.2, C21.2, C22.2, D1.2 (A), D8.2 (A), IC1.7 (GND), PWR1.2 (A), R6.2, R20.2; also elsewhere on the board
unnamed: C3.1, C4.1, C5.1, D2.1 (K), D23.1 (K), IC1.2 (Vin), R4.1
unnamed: C6.1, D1.1 (K), IC1.8 (PH), L1.1
unnamed: C6.2, IC1.1 (Boot)
unnamed: C7.1, IC1.4 (SS)
unnamed: C13.1, C21.1, IC1.6 (Comp)
unnamed: C13.2, R6.1
unnamed: IC1.3 (EN), R4.2
unnamed: IC1.5 (Vsense), R18.2, R19.1
unnamed: PWR1.1 (K), R10.2
unnamed: R19.2, R20.1
VUSB: D2.2 (A); also elsewhere on the board
V_in: F1.2; also elsewhere on the board

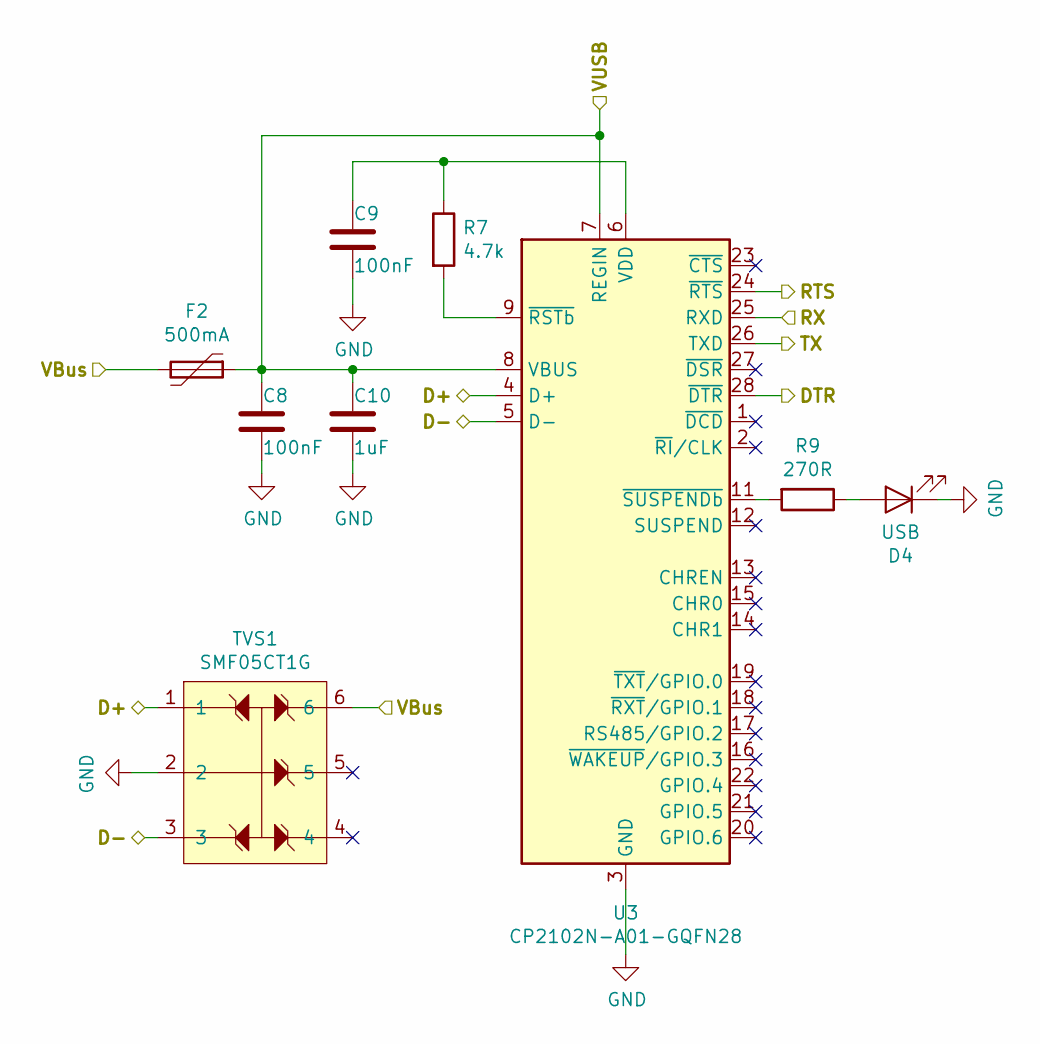
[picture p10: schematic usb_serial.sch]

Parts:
C8, C9: 100nF; C_0603_1608Metric; LCSC C14663
C10: 1uF; C_0603_1608Metric; LCSC C15849
D4: USB; D_0805_2012Metric; LCSC C2296
F2: 500mA; Fuse_1206_3216Metric; LCSC C69688
R7: 4.7k; R_0603_1608Metric; LCSC C23162
R9: 270R; R_0603_1608Metric; LCSC C22966
TVS1: SMF05CT1G; SOT-363_SC-70-6; LCSC C15879
U3: CP2102N-A01-GQFN28; QFN-28-1EP_5x5mm_P0.5mm_EP3.35x3.35mm; LCSC C6568

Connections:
/Reset circuitry/DTR: U3.28 (~DTR); also elsewhere on the board
/Reset circuitry/RTS: U3.24 (~RTS); also elsewhere on the board
/USB2Serial/D+: TVS1.1, U3.4 (D+); also elsewhere on the board
/USB2Serial/D-: TVS1.3, U3.5 (D-); also elsewhere on the board
/USB2Serial/VBus: F2.2, TVS1.6; also elsewhere on the board
GND: C8.1, C9.1, C10.1, D4.1 (K), TVS1.2, U3.3 (GND), U3.29 (GND); also elsewhere on the board
unnamed: C9.2, R7.1, U3.6 (VDD)
unnamed: D4.2 (A), R9.1
unnamed: R7.2, U3.9 (~RSTb)
unnamed: R9.2, U3.11 (~SUSPENDb)
RXD0: U3.26 (TXD); also elsewhere on the board
TXD0: U3.25 (RXD); also elsewhere on the board
VUSB: C8.2, C10.2, F2.1, U3.7 (REGIN), U3.8 (VBUS); also elsewhere on the board

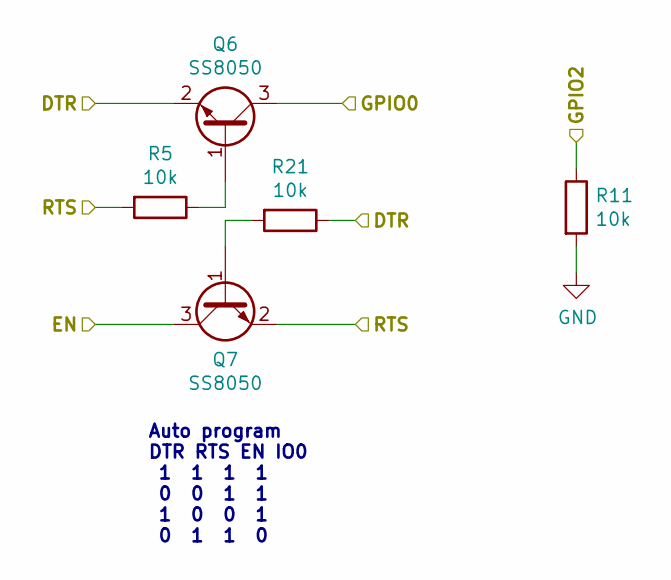
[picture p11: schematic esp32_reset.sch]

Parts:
Q6, Q7: SS8050; SOT-23; LCSC C2150
R5, R11, R21: 10k; R_0603_1608Metric; LCSC C25804

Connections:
/Reset circuitry/DTR: Q6.2 (E), R21.1; also elsewhere on the board
/Reset circuitry/RTS: Q7.2 (E), R5.2; also elsewhere on the board
EN: Q7.3 (C); also elsewhere on the board
GND: R11.2; also elsewhere on the board
GPIO0: Q6.3 (C); also elsewhere on the board
GPIO2: R11.1; also elsewhere on the board
unnamed: Q6.1 (B), R5.1
unnamed: Q7.1 (B), R21.2

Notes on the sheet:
Auto program DTR RTS EN IO0 1 1 1 1 0 0 1 1 1 0 0 1 0 1 1 0

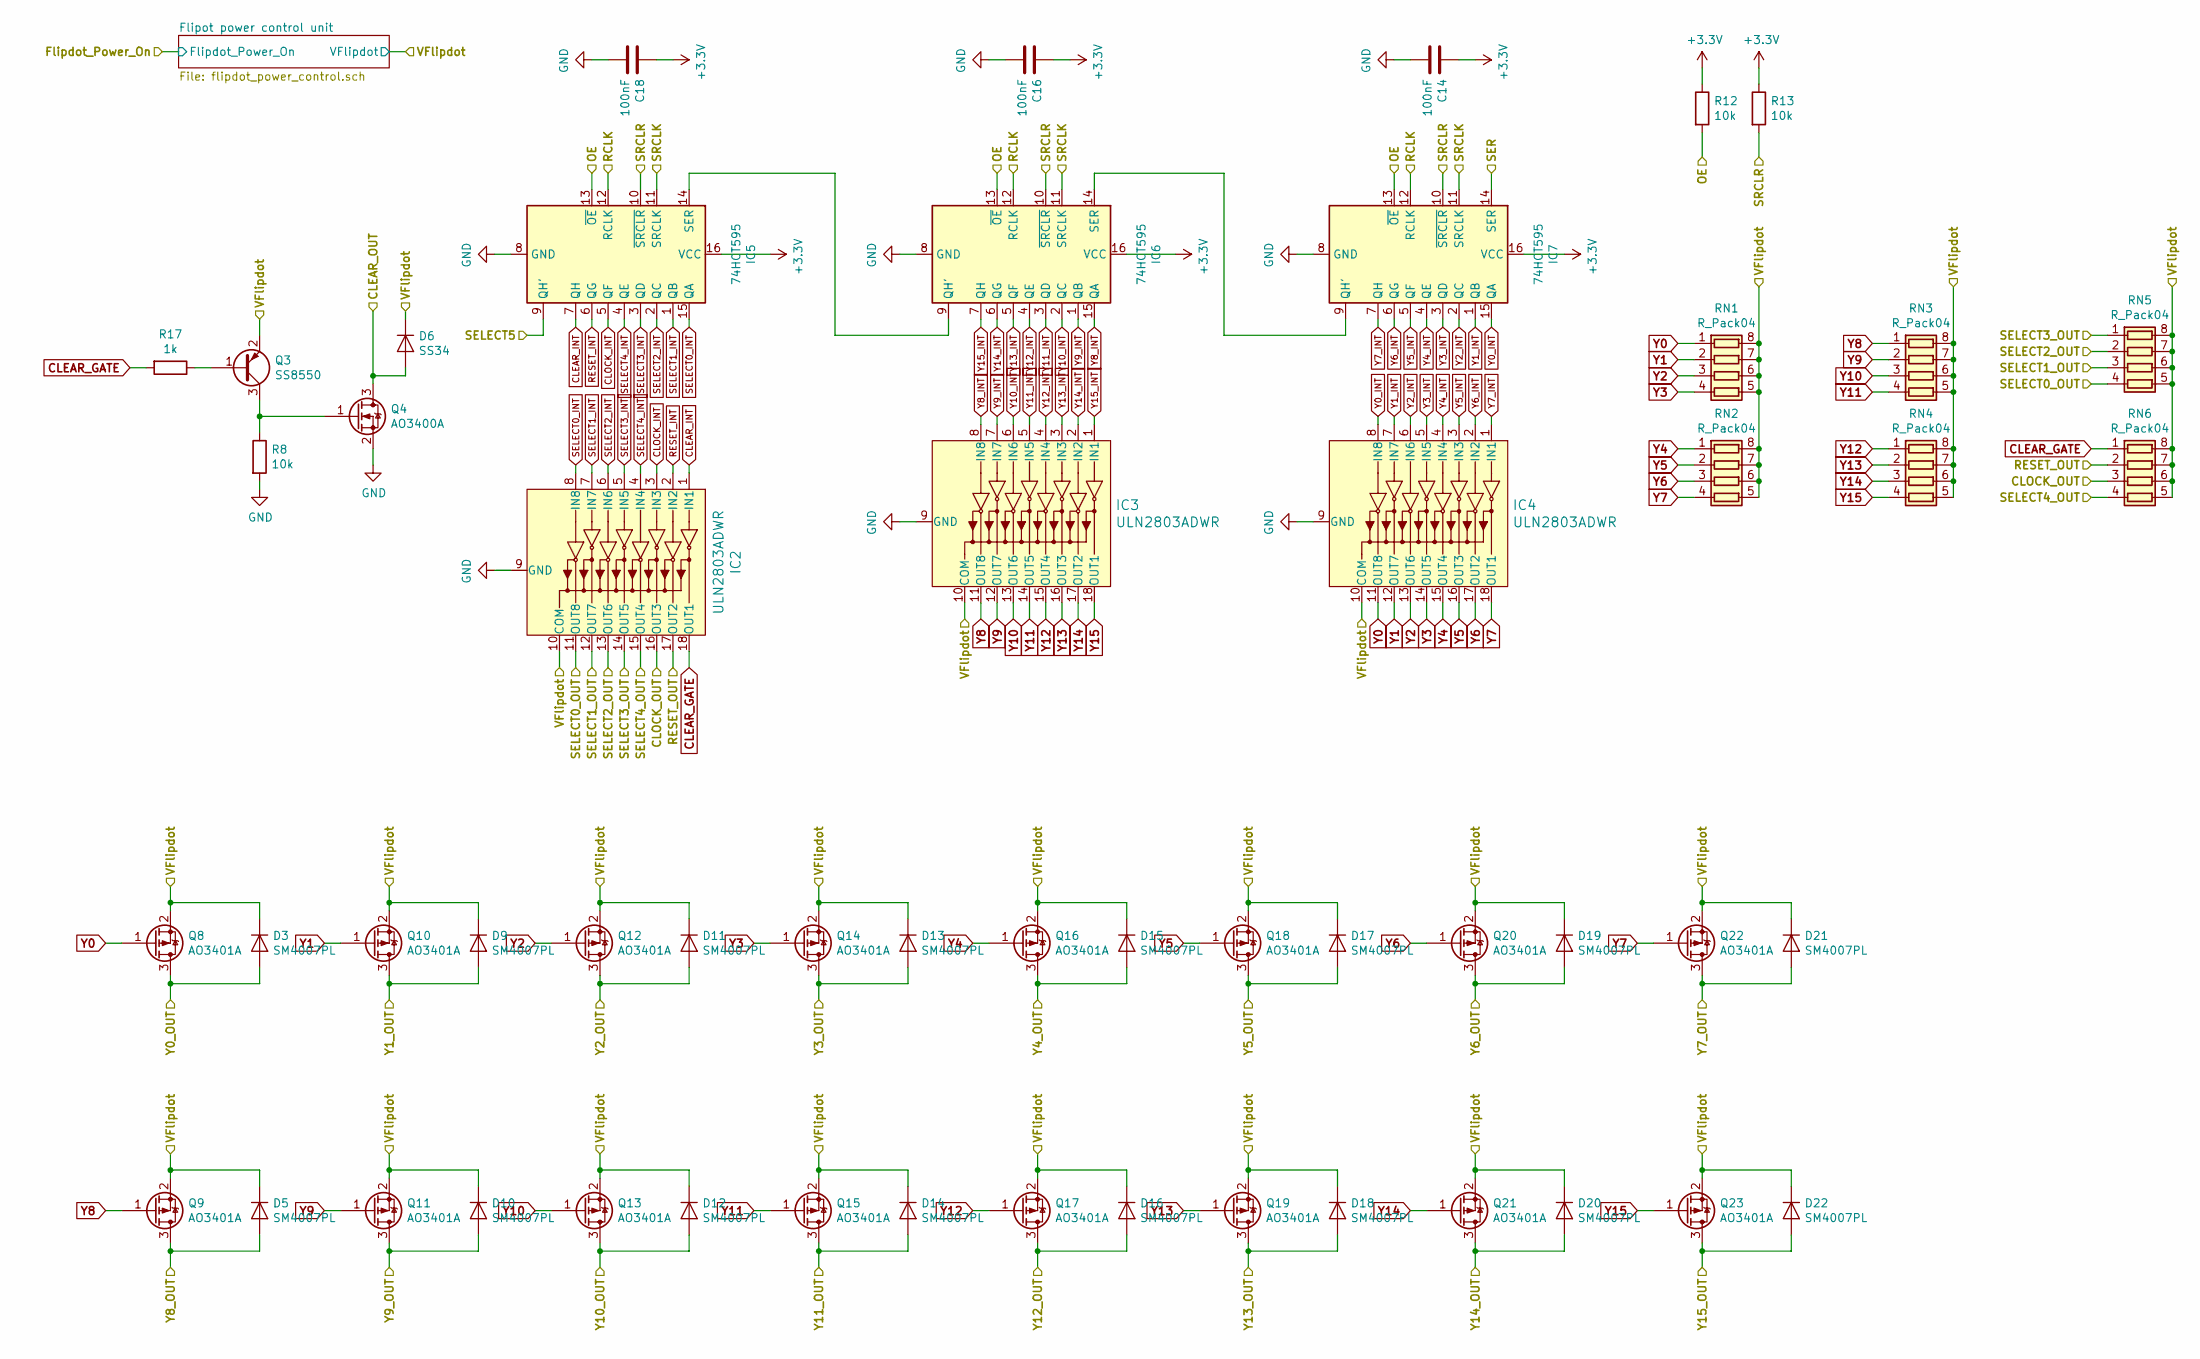
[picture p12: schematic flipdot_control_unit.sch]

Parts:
C14, C16, C18: 100nF; C_0603_1608Metric; LCSC C14663
D3, D5, D9, D10, D11, D12, D13, D14, D15, D16, D17, D18, D19, D20, D21, D22: SM4007PL; D_SOD-123F; LCSC C64898
D6: SS34; D_SMA; LCSC C84635
IC2, IC3, IC4: ULN2803ADWR; SOIC-18W_7.5x11.6mm_P1.27mm; MPN ULN2803ADWR; Digi-Key_PN 296-15777-1-ND
IC5, IC6, IC7: 74HCT595; SOIC-16_3.9x9.9mm_P1.27mm; LCSC C5613
Q3: SS8550; SOT-23; LCSC C8542
Q4: AO3400A; SOT-23; LCSC C20917
Q8, Q9, Q10, Q11, Q12, Q13, Q14, Q15, Q16, Q17, Q18, Q19, Q20, Q21, Q22, Q23: AO3401A; SOT-23; LCSC C15127
R8, R12, R13: 10k; R_0603_1608Metric; LCSC C25804
R17: 1k; R_0603_1608Metric; LCSC C21190
RN1, RN2, RN3, RN4, RN5, RN6: R_Pack04; R_Array_Convex_4x0603; LCSC C29718

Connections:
+3V3: C14.1, C16.1, C18.1, IC5.16 (VCC), IC6.16 (VCC), IC7.16 (VCC), R12.1, R13.1; also elsewhere on the board
CLEAR_GATE: IC2.18 (OUT1), R17.2, RN6.1 (R1.1)
CLEAR_INT: IC2.1 (IN1), IC5.7 (QH)
CLEAR_OUT: D6.2 (A), Q4.3 (D); also elsewhere on the board
CLOCK_INT: IC2.3 (IN3), IC5.5 (QF)
CLOCK_OUT: IC2.16 (OUT3), RN6.3 (R3.1); also elsewhere on the board
GND: C14.2, C16.2, C18.2, IC2.9 (GND), IC3.9 (GND), IC4.9 (GND), IC5.8 (GND), IC6.8 (GND), IC7.8 (GND), Q4.2 (S), R8.2; also elsewhere on the board
HSPI_MOSI: IC7.14 (SER); also elsewhere on the board
HSPI_SCLK: IC5.11 (SRCLK), IC6.11 (SRCLK), IC7.11 (SRCLK); also elsewhere on the board
HSPI_SS: IC5.13 (~OE), IC6.13 (~OE), IC7.13 (~OE), R12.2; also elsewhere on the board
unnamed: IC5.14 (SER), IC6.9 (QH')
unnamed: IC6.14 (SER), IC7.9 (QH')
unnamed: Q3.1 (B), R17.1
unnamed: Q3.3 (C), Q4.1 (G), R8.1
RCLK: IC5.12 (RCLK), IC6.12 (RCLK), IC7.12 (RCLK); also elsewhere on the board
RESET_INT: IC2.2 (IN2), IC5.6 (QG)
RESET_OUT: IC2.17 (OUT2), RN6.2 (R2.1); also elsewhere on the board
SELECT0_INT: IC2.8 (IN8), IC5.15 (QA)
SELECT0_OUT: IC2.11 (OUT8), RN5.4 (R4.1); also elsewhere on the board
SELECT1_INT: IC2.7 (IN7), IC5.1 (QB)
SELECT1_OUT: IC2.12 (OUT7), RN5.3 (R3.1); also elsewhere on the board
SELECT2_INT: IC2.6 (IN6), IC5.2 (QC)
SELECT2_OUT: IC2.13 (OUT6), RN5.2 (R2.1); also elsewhere on the board
SELECT3_INT: IC2.5 (IN5), IC5.3 (QD)
SELECT3_OUT: IC2.14 (OUT5), RN5.1 (R1.1); also elsewhere on the board
SELECT4_INT: IC2.4 (IN4), IC5.4 (QE)
SELECT4_OUT: IC2.15 (OUT4), RN6.4 (R4.1); also elsewhere on the board
SELECT5: IC5.9 (QH'); also elsewhere on the board
SRCLR: IC5.10 (~SRCLR), IC6.10 (~SRCLR), IC7.10 (~SRCLR), R13.2; also elsewhere on the board
VFlipdot: D3.1 (K), D5.1 (K), D6.1 (K), D9.1 (K), D10.1 (K), D11.1 (K), D12.1 (K), D13.1 (K), D14.1 (K), D15.1 (K), D16.1 (K), D17.1 (K), D18.1 (K), D19.1 (K), D20.1 (K), D21.1 (K), D22.1 (K), IC2.10 (COM), IC3.10 (COM), IC4.10 (COM), Q3.2 (E), Q8.2 (S), Q9.2 (S), Q10.2 (S), Q11.2 (S), Q12.2 (S), Q13.2 (S), Q14.2 (S), Q15.2 (S), Q16.2 (S), Q17.2 (S), Q18.2 (S), Q19.2 (S), Q20.2 (S), Q21.2 (S), Q22.2 (S), Q23.2 (S), RN1.5 (R4.2), RN1.6 (R3.2), RN1.7 (R2.2), RN1.8 (R1.2), RN2.5 (R4.2), RN2.6 (R3.2), RN2.7 (R2.2), RN2.8 (R1.2), RN3.5 (R4.2), RN3.6 (R3.2), RN3.7 (R2.2), RN3.8 (R1.2), RN4.5 (R4.2), RN4.6 (R3.2), RN4.7 (R2.2), RN4.8 (R1.2), RN5.5 (R4.2), RN5.6 (R3.2), RN5.7 (R2.2), RN5.8 (R1.2), RN6.5 (R4.2), RN6.6 (R3.2), RN6.7 (R2.2), RN6.8 (R1.2); also elsewhere on the board
Y0: IC4.11 (OUT8), Q8.1 (G), RN1.1 (R1.1)
Y0_INT: IC4.8 (IN8), IC7.15 (QA)
Y0_OUT: D3.2 (A), Q8.3 (D); also elsewhere on the board
Y1: IC4.12 (OUT7), Q10.1 (G), RN1.2 (R2.1)
Y1_INT: IC4.7 (IN7), IC7.1 (QB)
Y1_OUT: D9.2 (A), Q10.3 (D); also elsewhere on the board
Y2: IC4.13 (OUT6), Q12.1 (G), RN1.3 (R3.1)
Y2_INT: IC4.6 (IN6), IC7.2 (QC)
Y2_OUT: D11.2 (A), Q12.3 (D); also elsewhere on the board
Y3: IC4.14 (OUT5), Q14.1 (G), RN1.4 (R4.1)
Y3_INT: IC4.5 (IN5), IC7.3 (QD)
Y3_OUT: D13.2 (A), Q14.3 (D); also elsewhere on the board
Y4: IC4.15 (OUT4), Q16.1 (G), RN2.1 (R1.1)
Y4_INT: IC4.4 (IN4), IC7.4 (QE)
Y4_OUT: D15.2 (A), Q16.3 (D); also elsewhere on the board
Y5: IC4.16 (OUT3), Q18.1 (G), RN2.2 (R2.1)
Y5_INT: IC4.3 (IN3), IC7.5 (QF)
Y5_OUT: D17.2 (A), Q18.3 (D); also elsewhere on the board
Y6: IC4.17 (OUT2), Q20.1 (G), RN2.3 (R3.1)
Y6_INT: IC4.2 (IN2), IC7.6 (QG)
Y6_OUT: D19.2 (A), Q20.3 (D); also elsewhere on the board
Y7: IC4.18 (OUT1), Q22.1 (G), RN2.4 (R4.1)
Y7_INT: IC4.1 (IN1), IC7.7 (QH)
Y7_OUT: D21.2 (A), Q22.3 (D); also elsewhere on the board
Y8: IC3.11 (OUT8), Q9.1 (G), RN3.1 (R1.1)
Y8_INT: IC3.8 (IN8), IC6.15 (QA)
Y8_OUT: D5.2 (A), Q9.3 (D); also elsewhere on the board
Y9: IC3.12 (OUT7), Q11.1 (G), RN3.2 (R2.1)
Y9_INT: IC3.7 (IN7), IC6.1 (QB)
Y9_OUT: D10.2 (A), Q11.3 (D); also elsewhere on the board
Y10: IC3.13 (OUT6), Q13.1 (G), RN3.3 (R3.1)
Y10_INT: IC3.6 (IN6), IC6.2 (QC)
Y10_OUT: D12.2 (A), Q13.3 (D); also elsewhere on the board
Y11: IC3.14 (OUT5), Q15.1 (G), RN3.4 (R4.1)
Y11_INT: IC3.5 (IN5), IC6.3 (QD)
Y11_OUT: D14.2 (A), Q15.3 (D); also elsewhere on the board
Y12: IC3.15 (OUT4), Q17.1 (G), RN4.1 (R1.1)
Y12_INT: IC3.4 (IN4), IC6.4 (QE)
Y12_OUT: D16.2 (A), Q17.3 (D); also elsewhere on the board
Y13: IC3.16 (OUT3), Q19.1 (G), RN4.2 (R2.1)
Y13_INT: IC3.3 (IN3), IC6.5 (QF)
Y13_OUT: D18.2 (A), Q19.3 (D); also elsewhere on the board
Y14: IC3.17 (OUT2), Q21.1 (G), RN4.3 (R3.1)
Y14_INT: IC3.2 (IN2), IC6.6 (QG)
Y14_OUT: D20.2 (A), Q21.3 (D); also elsewhere on the board
Y15: IC3.18 (OUT1), Q23.1 (G), RN4.4 (R4.1)
Y15_INT: IC3.1 (IN1), IC6.7 (QH)
Y15_OUT: D22.2 (A), Q23.3 (D); also elsewhere on the board

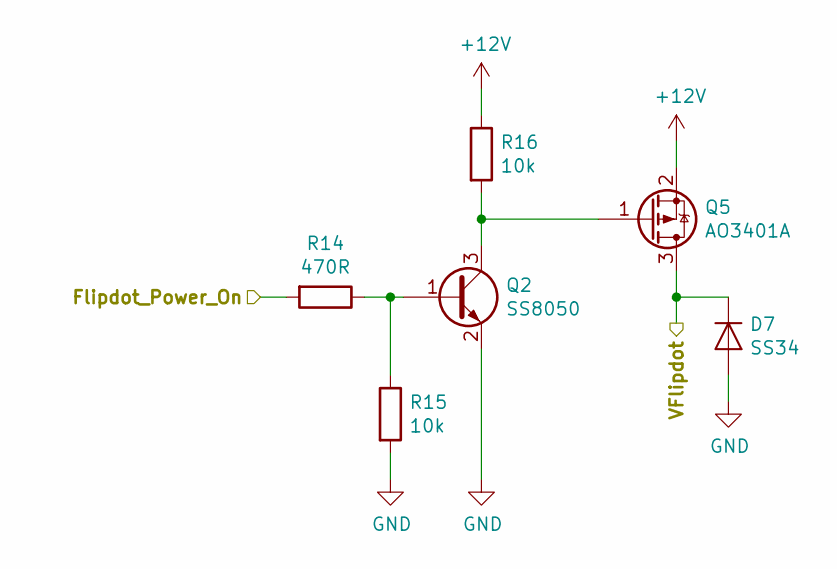
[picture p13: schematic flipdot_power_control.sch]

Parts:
D7: SS34; D_SMA; LCSC C84635
Q2: SS8050; SOT-23; LCSC C2150
Q5: AO3401A; SOT-23; LCSC C15127
R14: 470R; R_0603_1608Metric; LCSC C23179
R15, R16: 10k; R_0603_1608Metric; LCSC C25804

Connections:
+12V: Q5.2 (S), R16.1; also elsewhere on the board
FLIPDOT_PWR: R14.2; also elsewhere on the board
GND: D7.2 (A), Q2.2 (E), R15.2; also elsewhere on the board
unnamed: Q2.1 (B), R14.1, R15.1
unnamed: Q2.3 (C), Q5.1 (G), R16.2
VFlipdot: D7.1 (K), Q5.3 (D); also elsewhere on the board

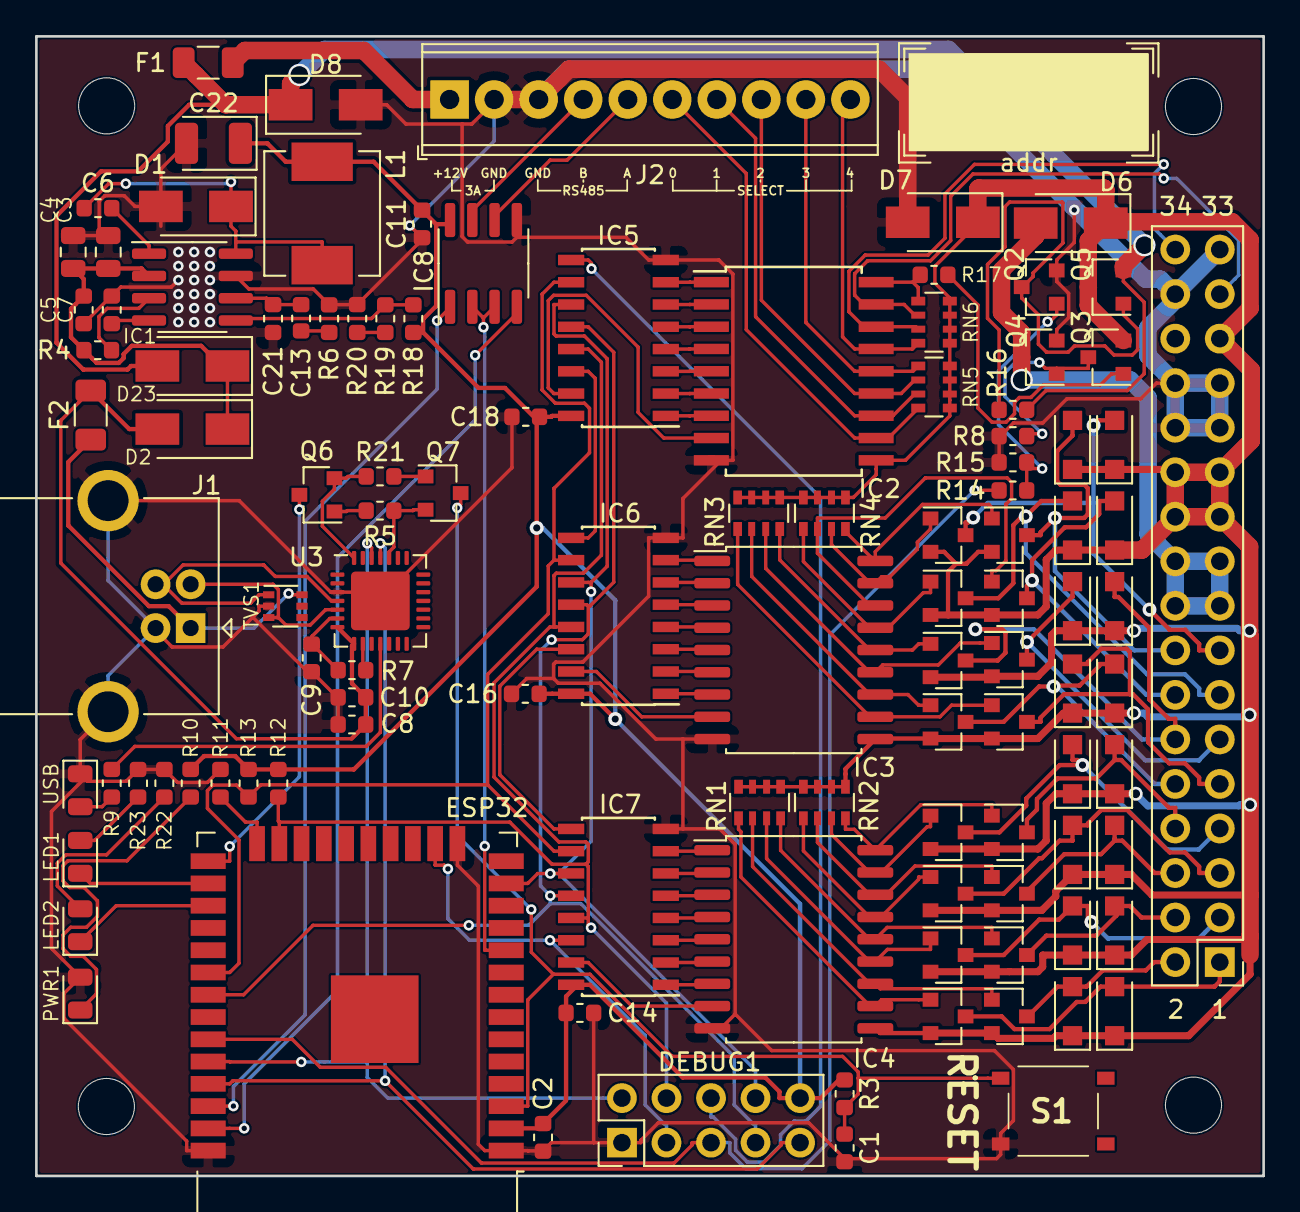
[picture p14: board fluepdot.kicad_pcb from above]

Board: 2 copper layers, 70.0 x 65.0 mm, 115 parts (0 on the bottom side), 119 nets.

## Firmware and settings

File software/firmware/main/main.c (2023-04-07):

#include "console.h"
#include "main.h"
#include "mdns_util.h"
#include "httpd.h"
#include "util.h"
#include "raw_api.h"

#include "freertos/FreeRTOS.h"
#include "esp_event.h"
#include "esp_log.h"
#include "nvs_flash.h"

static const char* TAG = "main.c";

system_configuration_t system_configuration;
flipdot_t flipdot;
httpd_handle_t httpd_server;
wifi_t wifi;

static esp_err_t initialize() {
    // initialize non-volatile storage
    esp_err_t err = nvs_flash_init();
    if (err == ESP_ERR_NVS_NO_FREE_PAGES || err == ESP_ERR_NVS_NEW_VERSION_FOUND) {
        ESP_ERROR_CHECK(nvs_flash_erase());
        err = nvs_flash_init();
    }
    ERROR_CHECK(err);

    // Initialize the TCP/IP stack.
    ERROR_CHECK(esp_netif_init());

    // Create default event loop
    ERROR_CHECK(esp_event_loop_create_default());

    return ESP_OK;
}

void app_main() {
    ESP_LOGI(TAG, "Flipdot firmware, git commit %s", GIT_SHA1);

    // global initializations
    ESP_ERROR_CHECK(initialize());

    // load the system configuration
    ESP_ERROR_CHECK(system_configuration_load(&system_configuration));
    ESP_LOGI(TAG, "System configuration loaded");
    
    // intialize the interactive console
    ERROR_SHOW(console_initialize(&system_configuration));
    ESP_LOGI(TAG, "console initialized");


    // initialize wireless connections
    ERROR_SHOW(wifi_initialize(&wifi, &system_configuration.wifi, system_configuration.hostname));
    ESP_LOGI(TAG, "WiFi initialized");

    // initialize mDNS
    ERROR_SHOW(mdns_initialize(system_configuration.hostname));
    ESP_LOGI(TAG, "mDNS initialized");

    // TODO initialize wired connections

    // initialize the flipdot
    ERROR_SHOW(flipdot_initialize(&flipdot, &system_configuration.flipdot));
    ESP_LOGI(TAG, "Flipdot initialized");

    // power on the flipdot
    ERROR_SHOW(flipdot_set_power(&flipdot, true));
    ESP_LOGI(TAG, "Flipdot powered up");

    // initialize the webserver
    ERROR_SHOW(httpd_initialize(httpd_server));
    ESP_LOGI(TAG, "httpd initialized");

    ERROR_SHOW(raw_api_initialize());
    ESP_LOGI(TAG, "raw api initialized");

    while (true) {
        vTaskDelay(500 * portTICK_PERIOD_MS);
    }
}

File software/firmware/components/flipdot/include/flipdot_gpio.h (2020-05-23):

/**
  * @file
  * @brief Flipdot GPIO abstraction
  */

#pragma once

#include <stdint.h>
#include <stdbool.h>

/**
  * @brief GPIO pin for flipdot power on
  * Setting this GPIO to high switches Q5 using Q2, providing +12V on VFlipdot
  */
#define FLIPDOT_GPIO_PWR_ON (21)

/**
  * @brief Not connected
  * Reading from SPI is not required and results in undefined behaviour as GPIO12 is left floating.
  */
#define FLIPDOT_GPIO_SPI_MISO (12)

/**
  * @brief GPIO pin for flipdot driver registers SER
  * @note SPI is used for controlling registers IC5, IC6 and IC7
  */
#define FLIPDOT_GPIO_SPI_MOSI (13)

/**
  * @brief GPIO pin for flipdor driver registers SRCLK
  * @note SPI is used for controlling registers IC5, IC6 and IC7
  */
#define FLIPDOT_GPIO_SPI_CLK (14)

/**
  * @brief GPIO pin for flipdor driver registers RCLK
  */
#define FLIPDOT_GPIO_RCLK_PIN (19)

/**
  * @brief GPIO pin for flipdot driver registers SCRLR
  */
#define FLIPDOT_GPIO_SRCLR_PIN (18)

/**
  * @brief GPIO pin for flipdot drive registers OE
  */
#define FLIPDOT_GPIO_OE_PIN (15)

/**
  * @brief SPI clock rate
  * @note According to datasheet 8 MHz is within guaranteed limit
  */
#define FLIPDOT_SPI_SPEED_HZ (8 * 1000 * 1000)

/**
  * @brief Bit pattern for selecting no panel
  */
#define FLIPDOT_NO_SELECT (0b00011111)

/**
  * @brief Flipdot driver registers pin out
  * Shift registers IC5, IC6 and IC7 are used as port expansion for the ESP32.
  * This data structure memory maps the pins to human readable code
  */
typedef struct {
    /**
      * @brief values of SELECT[0..4]
      * Setting a single bit to zero causes the corresponding panel select (J2 pin 6..10) to be pulled to +12V.
      * Otherwise driven to GND by IC2.
      * @note Only one panel should be selected at a time, to account for the maximum amount of power the flipdot PCB can drive.
      */
    uint8_t select : 5;

    /**
      * @brief clock signal (inverted)
      * Setting this to zero pulls J3 pin 34 to +12V.
      * Otherwise driven to GND by IC2.
      */
    bool clock : 1;

    /**
      * @brief reset signal (inverted)
      * Setting this to zero pulls J3 pin 31 to +12V.
      * Otherwise driven to GND by IC2.
      */
    bool reset : 1;

    /**
      * @brief column clear driver
      * Setting this to one causes low-side driver Q4 to drive common clear (J3 17..20) to GND.
      * The low-side driver is used to clear a whole column.
      * @note: You must never drive a row and clear at once, as this will blow fuse F1.
      */
    bool clear : 1;

    /**
      * @brief column row driver values
      * 16 row high side driver allow for setting individual pixels.
      * @note: You must never drive a row and clear at once, as this will blow fuse F1.
      */
    uint16_t rows : 16;
} __attribute__((packed)) flipdot_io_state_t;

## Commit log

2019-08-09 Added hardware and artworks
    [esp32_reset.sch, flipdot_power_control.sch, fluepdot.kicad_pcb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]
2019-08-11 Fix #1
    [usb_serial.sch]
2019-10-26 Commit jlcpcb compatible version
    [esp32_reset.sch, flipdot_control_unit.sch, flipdot_power_control.sch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]
2019-11-08 Add CAD files for installation at #36C3
    [hexagon.scad]
2019-11-08 Add stl file for installation
    [hexagon.stl]
2019-12-14 Commit current status of the firmware
2019-12-14 Added OTA update functionality
    [partitions.csv]
2020-01-10 Add some examples
    [beat.csv, bsod.csv, fluepdot.csv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]
2020-04-19 Post congress lobotomy and clean up
    [beat.csv, bsod.csv, fluepdot.csv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]
2020-05-23 Added 'flipdot_clear' and 'config_panel_layout' commands
    [console.c]
2020-05-24 More badges 🥰
2020-06-21 Added production files
    [fluepdot-B_Cu.gbr, fluepdot-B_Mask.gbr, fluepdot-B_Paste.gbr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]
2020-06-21 Do not fail hard on startup on wifi config, etc.
    [main.c]
2020-06-21 Fix stage order
2020-06-24 Fix a stupid bug 🤦
2020-06-24 Fix broken docs stage
2020-06-25 Added font rendering API endpoint 🅰️🅱️🅲
2020-07-10 Updated production files
    [bom.csv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]
2020-12-10 Replace wrong 74HC165 by 74HC595
    [bom.csv]

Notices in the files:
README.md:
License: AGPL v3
